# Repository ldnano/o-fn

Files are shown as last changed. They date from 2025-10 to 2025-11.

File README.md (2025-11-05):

<div align="center">

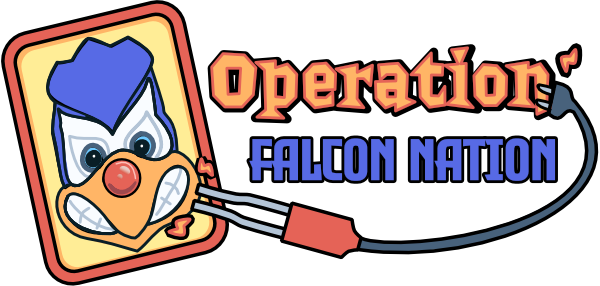
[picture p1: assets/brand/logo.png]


<h1>Operation: Falcon Nation</h1>

🦅 An automated board game reimagining which elevates scale, sensory experience, and interactivity. Featuring a life-size gameboard, themed pieces, and game mechanics, the project serves philanthropic causes and events.

----------------------------------
</div>

<details>
<summary><kbd>Table of contents</kbd></summary>

#### TOC

- [✨ Features](#-features)
- [🚀 Usage](#-urage)
  - [How to Operate](#how-to-operate)
  - [Game Mode Overview](#game-mode-overview)
  - [How to Play](#how-to-play)
- [📊 Flowcharts](#-flowcharts)
  - [Logic](#logic-)
  - [GUI](#gui-)
  - [Debugging](#debugging-)
- [🍱 Piece/Cavity Descriptions](#-piece-cavity-descriptions)
  - [List of pieces](#list-of-pieces)
  - [Cavity Anatomy](#cavity-anatomy)
- [💾 Programming Documentation](#-programming-documentation)
  - [Tasks](#tasks)
  - [Function Blocks](#function-blocks)
  - [Variables](#variables)
- [🔌 Electrical Wiring Diagram](#-electrical-wiring-diagram)
- [🗺 Monorepo Layout](#-monorepo-layout)

####

</details>

## ✨ Features

* Automatic piece-removal detection
* Circuit-based tong penalty loop
* Score-keeping and dynamic leaderboards
* Haptic-feedback-enabled modified kitchen tongs
* Multicolor board-and-cavity game state lights
* 11 custom-themed game pieces & cavities
* Two touchscreen web panel displays
* Two (repurposed car) speakers & immersive audio
* Plug-and-outlet power for project & tongs

## 🚀 Usage

### How to Operate

1. Plug in the power input located near the red switch on the left wall of the project, positioned closest near the falcon's head.
2. Press the red power switch located next to the power input and confirm that fans, web panels, and PLC (through glass) are powered and/or booting.
3. When the panel begins to display timers (typically 5 second countdowns), wait until a new calibration page with "LEFT" and "RIGHT" buttons. On the left panel, press "LEFT" and on the right one press "RIGHT".
4. The next page will be a sensor setup page that will indicate for which cavities the sensors are currently detecting a piece.
5. When all pieces are detected or early if necessary (pieces are lost, sensors are broken), press start and you will be navigated to the home (splash) screen.
6. From here, select a game mode and proceed through the steps of inputting player count, "nicknames", and confirmation.
7. Proceed to play Operation: Falcon Nation!

### Game Mode Overview

#### Demo Mode
In demo mode, a simplified "classic" mode variant, only four of the game's eleven total pieces are enabled, allowing a faster, more streamlined experience for showcases and demonstrations of the project.

#### Multiplayer (Classic) Mode
This version of the game operates most similarly to the original game, with all pieces activated. Without a stopwatch, the goal of this game is to compete for the highest monetary score.

#### Singleplayer (Blitz) Mode
As a singleplayer game, players of blitz mode aim to remove every piece in the least (or record) possible amount of time.

### How to Play

1. Presuming that game has been calibrated and configured, a "Play Game" button would become active on the left web panel screen.
2. When this button is clicked, the main game screen will appear, with the first player's piece assignment being displayed on the left panel and the initial (blank) leaderboard on the right.
3. This player must now attempt to take the assigned piece out of its cavity. If they fail, red lights will shine but if they succeed, green lights.
4, The leaderboard on the right will update with money counts accordingly and the "end game" button allows the game to be exited early.
5. When the game ends and the deck has been emptied, the final leaderboard and a thank you message will appear.

## 📊 Flowcharts

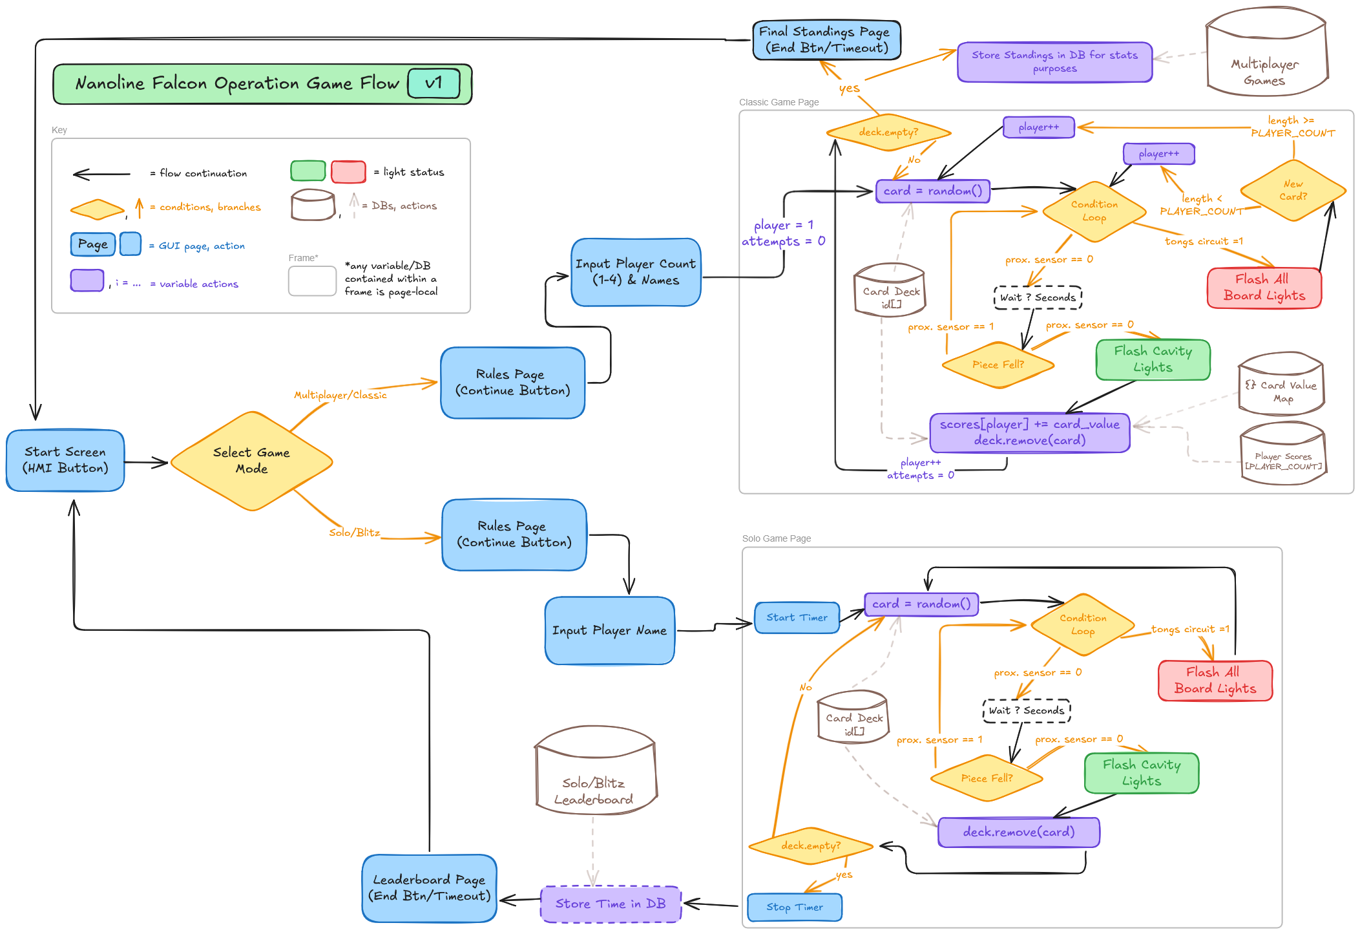
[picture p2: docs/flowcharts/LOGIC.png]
### <details><summary>Logic</summary> </details>

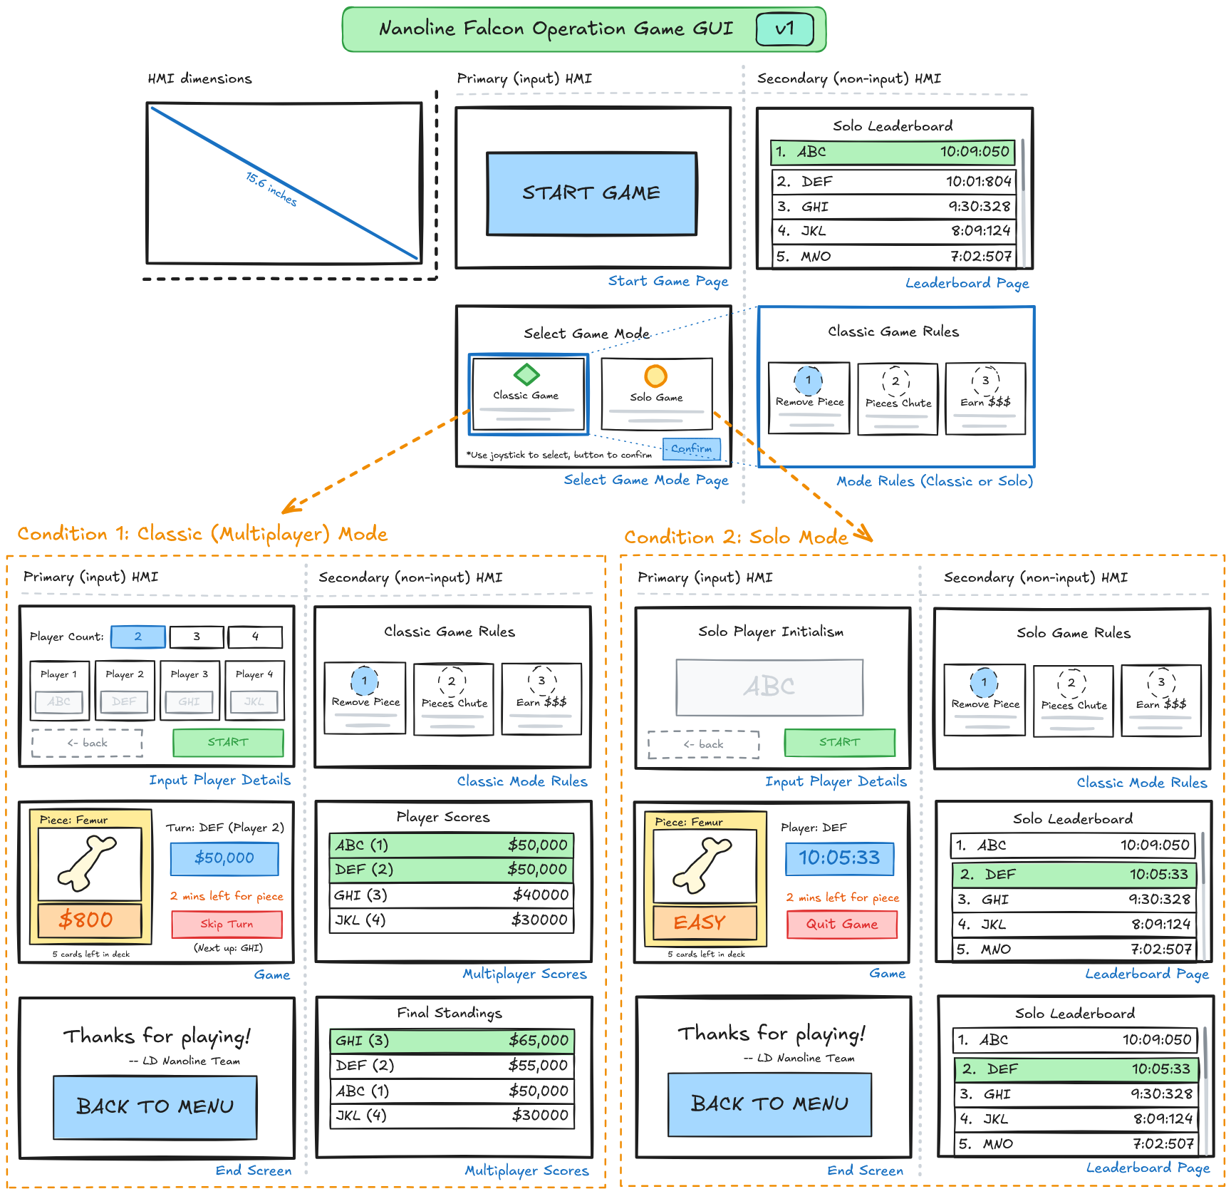
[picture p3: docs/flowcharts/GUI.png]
### <details><summary>GUI</summary> </details>

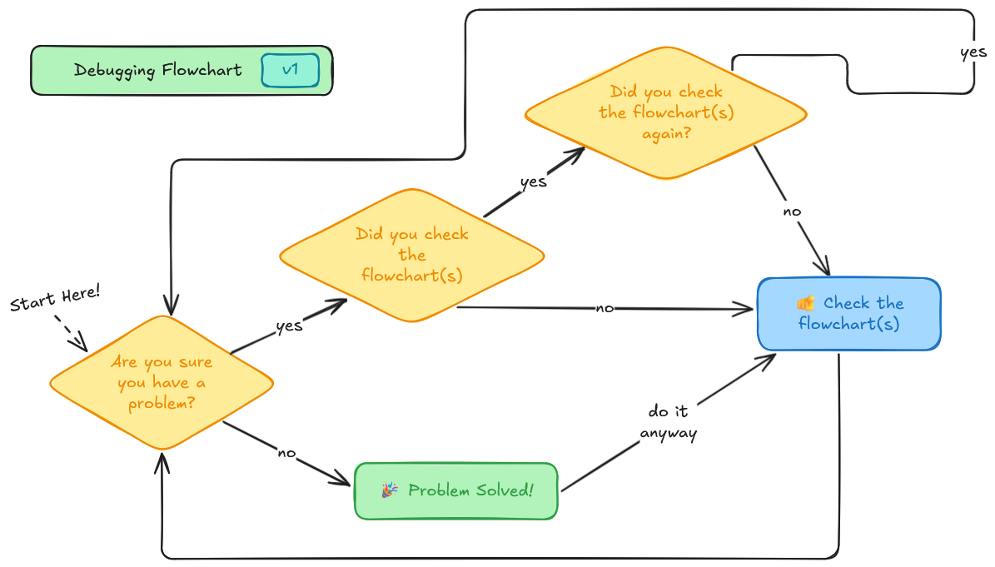
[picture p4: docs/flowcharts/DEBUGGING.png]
### <details><summary>Debugging</summary> </details>

## 🍱 Piece/Cavity Descriptions

### List of Pieces

| Piece Icon | Card Design | Name | Game Value |
|---|---|---|---|
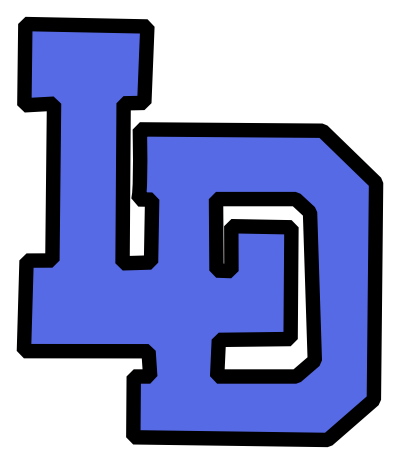
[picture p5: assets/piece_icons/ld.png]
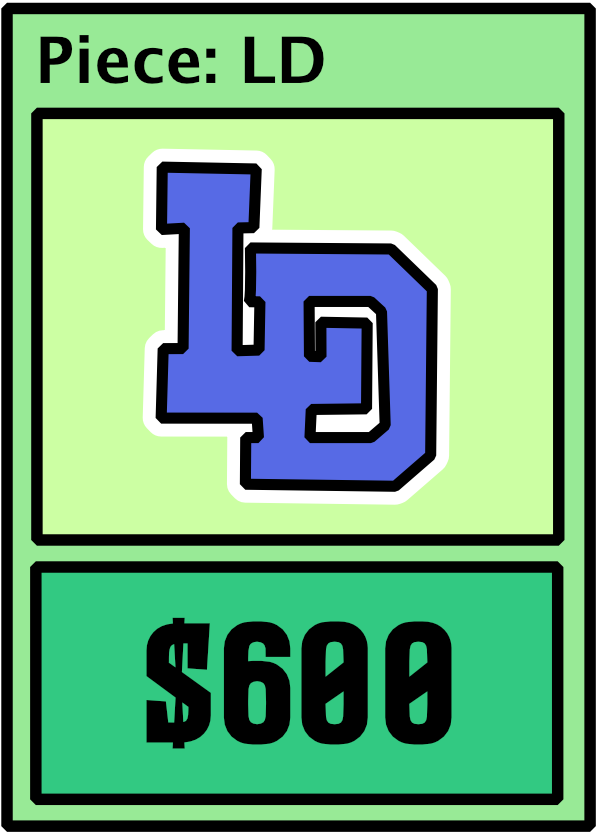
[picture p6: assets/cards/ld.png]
|  |  | LD Insignia | $600 |
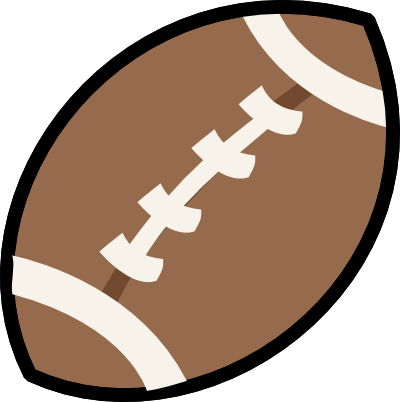
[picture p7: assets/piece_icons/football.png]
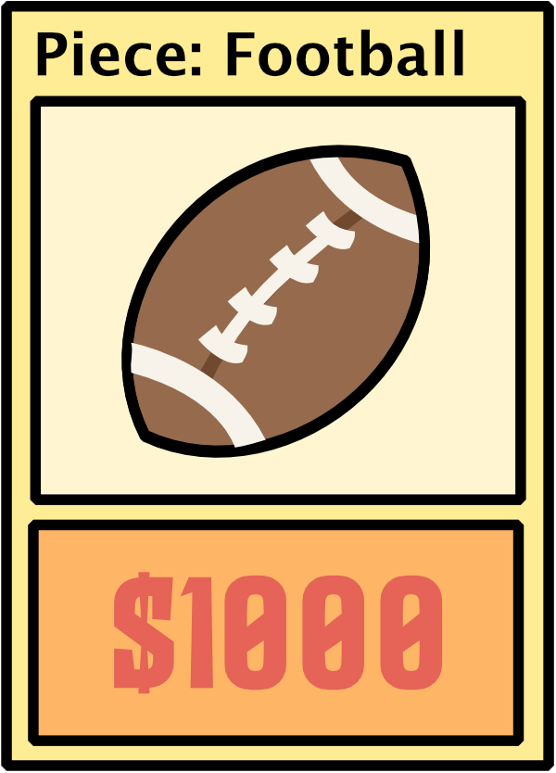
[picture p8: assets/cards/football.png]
|  |  | Football | $1000 |
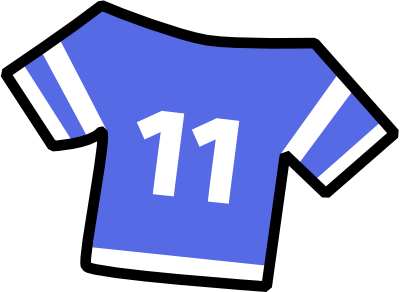
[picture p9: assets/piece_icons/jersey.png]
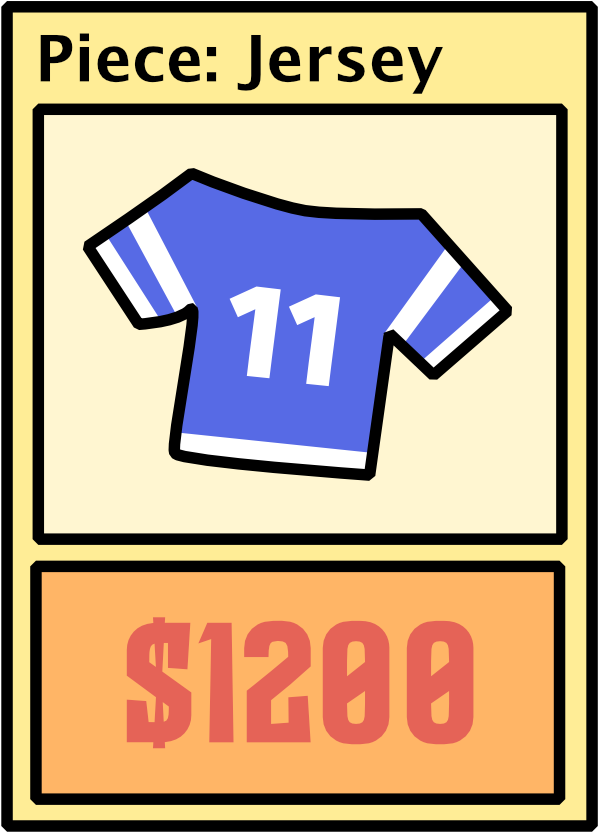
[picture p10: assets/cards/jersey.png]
|  |  | Jersey | $1200 |
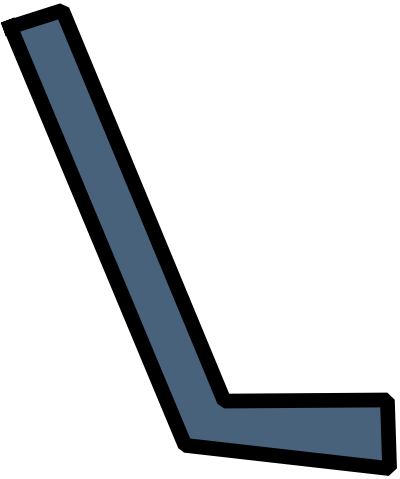
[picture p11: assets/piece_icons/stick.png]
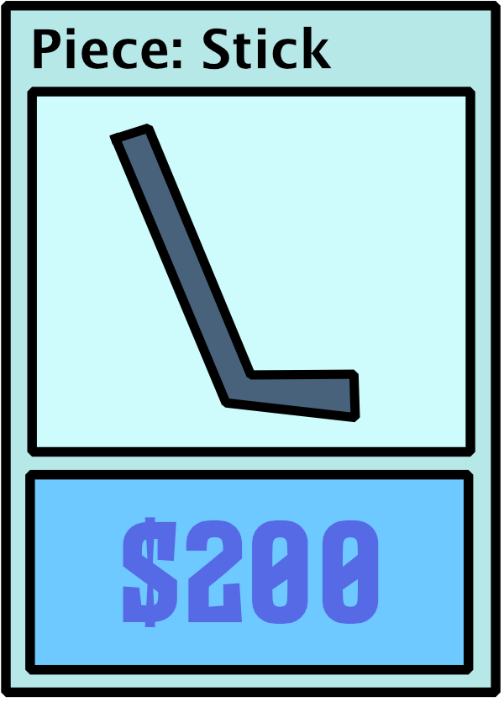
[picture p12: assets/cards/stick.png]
|  |  | Hockey Stick | $200 |
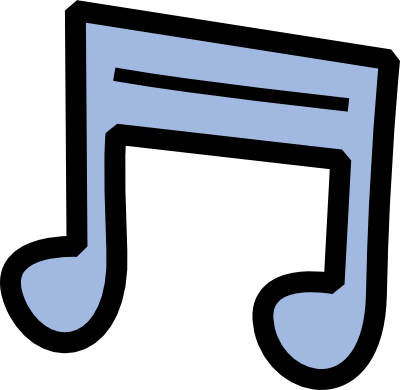
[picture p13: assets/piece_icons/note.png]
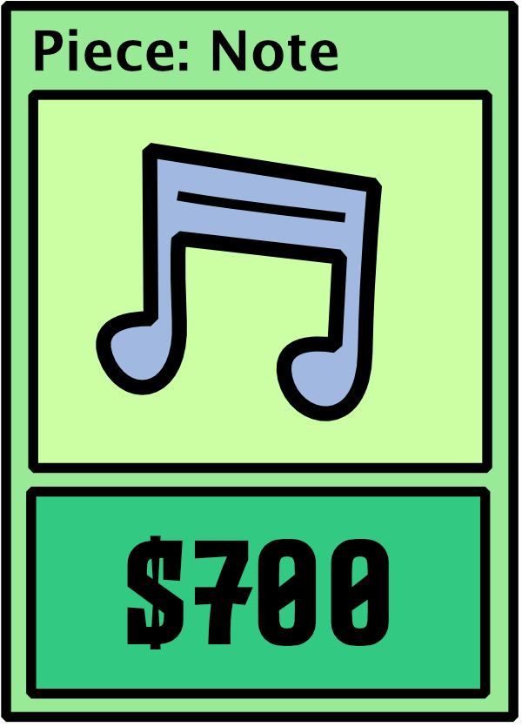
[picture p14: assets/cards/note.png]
|  |  | Music Note | $700 |
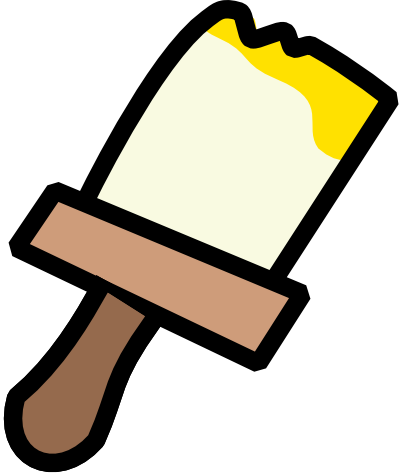
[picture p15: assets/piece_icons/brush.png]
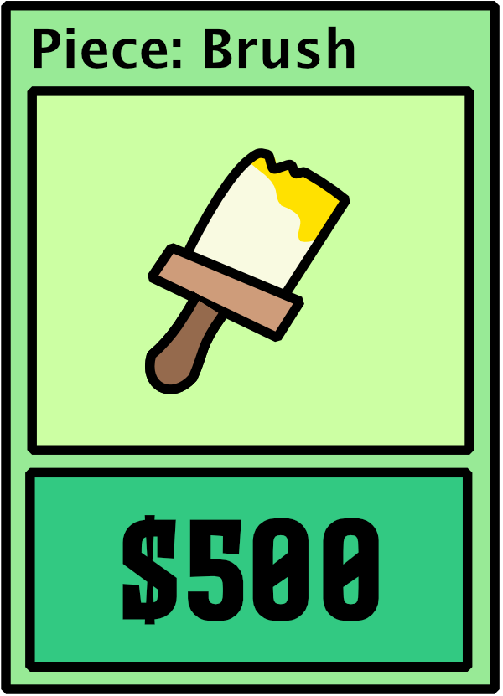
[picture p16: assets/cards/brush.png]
|  |  | Paintbrush | $500 |
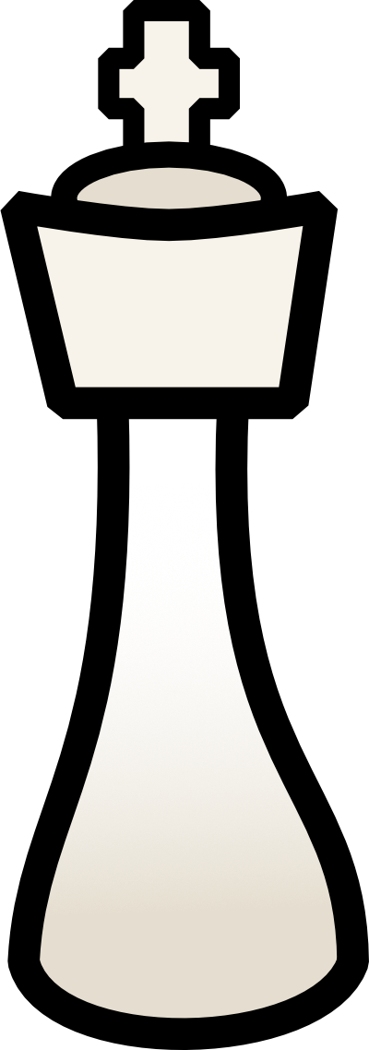
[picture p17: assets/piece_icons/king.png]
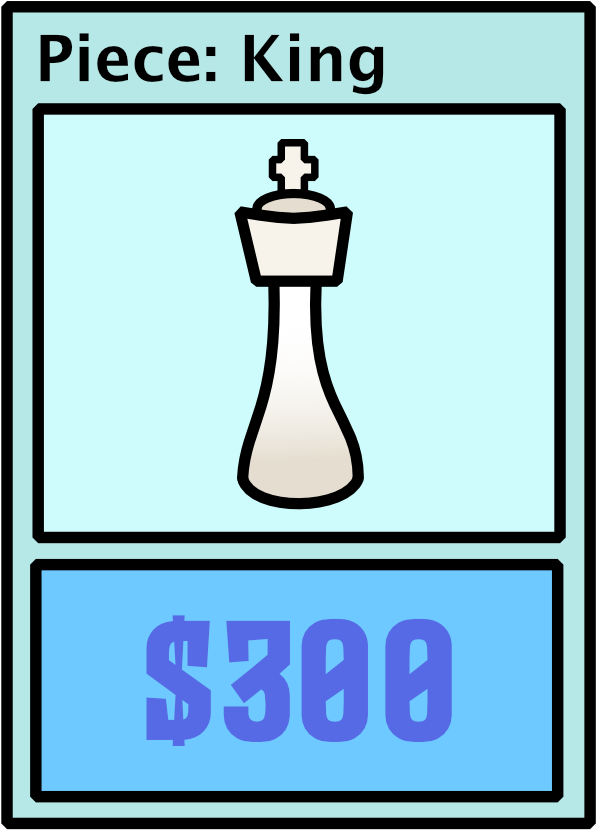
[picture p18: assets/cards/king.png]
|  |  | Chess King | $300 |
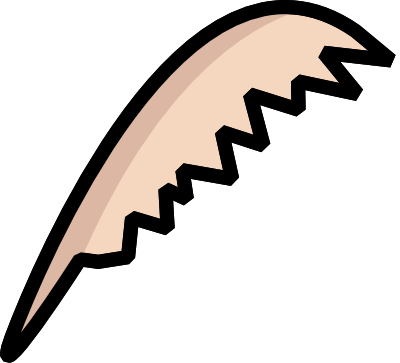
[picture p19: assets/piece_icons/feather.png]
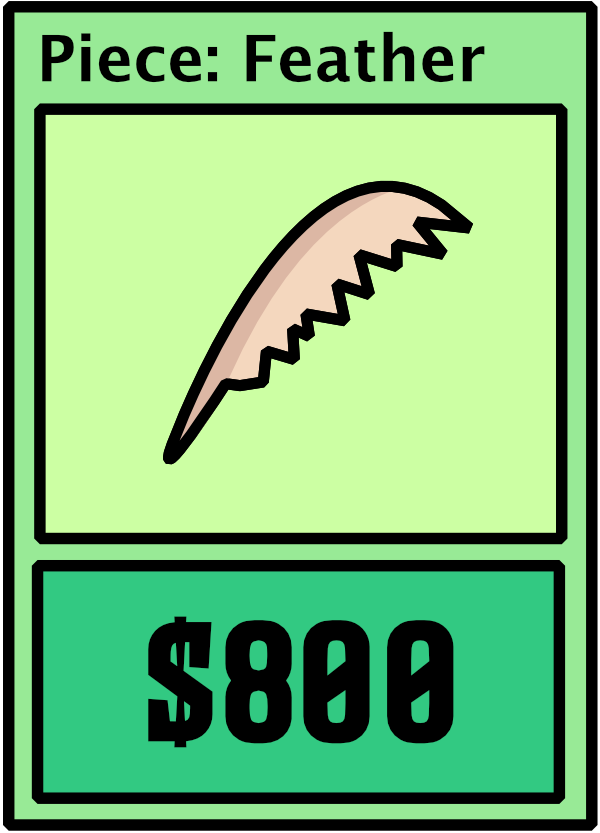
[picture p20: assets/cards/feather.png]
|  |  | Feather | $800 |
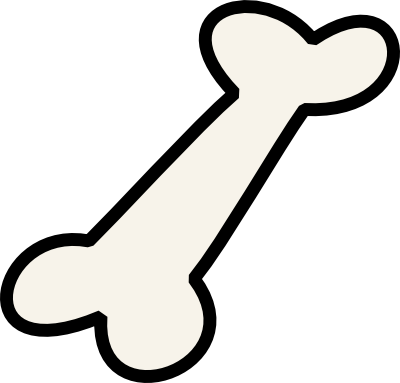
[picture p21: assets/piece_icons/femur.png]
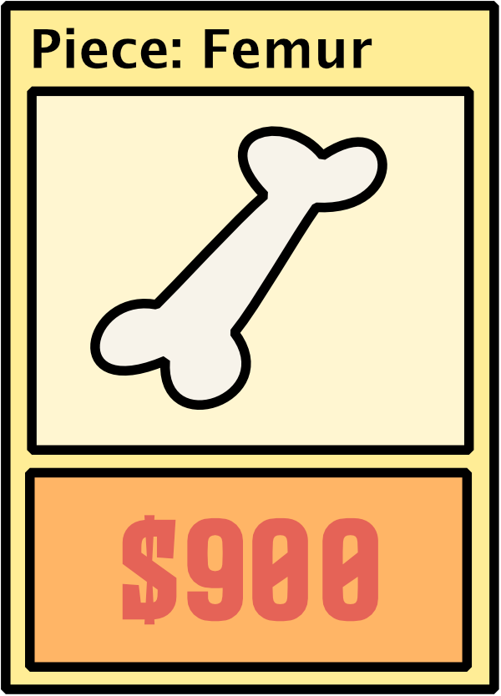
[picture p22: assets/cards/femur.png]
|  |  | Bone | $900 |
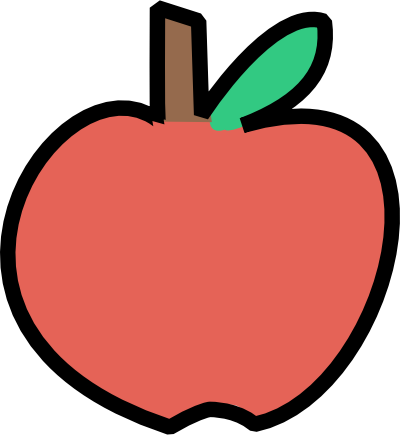
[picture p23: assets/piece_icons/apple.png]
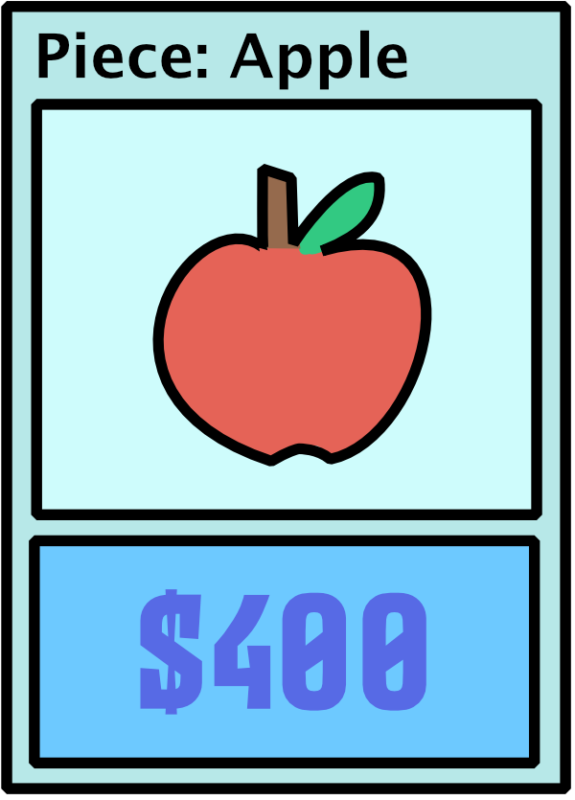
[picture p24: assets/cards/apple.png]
|  |  | Apple | $400 |
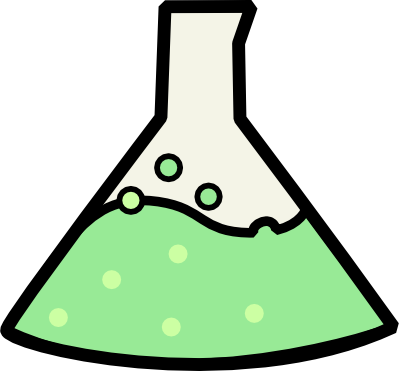
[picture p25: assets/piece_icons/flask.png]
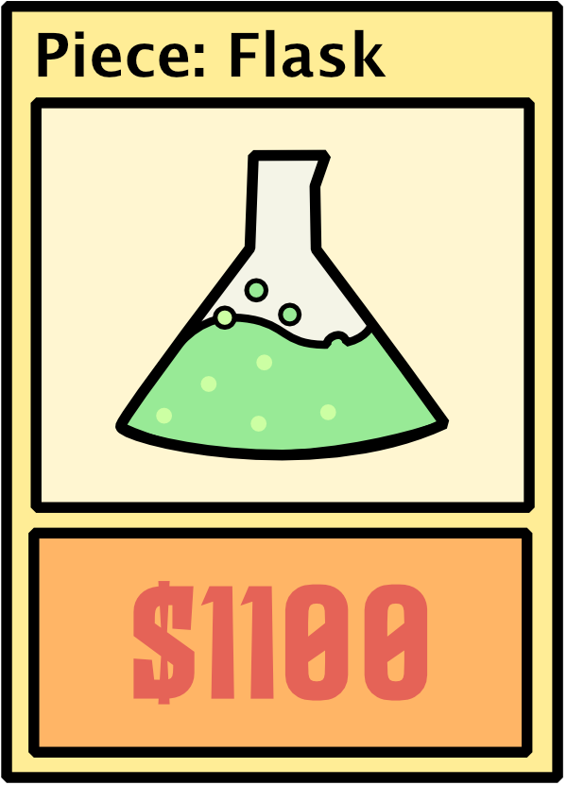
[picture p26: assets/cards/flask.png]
|  |  | Flask | $1100 |

### Cavity Anatomy

(Top-to-bottom)

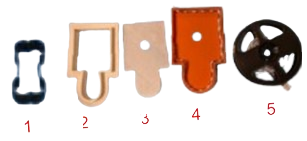
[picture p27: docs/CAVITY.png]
Cavity Diagram


1. Conductive Cavity Wall
2. Cavity Bracket
3. Clear "Light Refractor" Panel
4. Cavity Light Shell
5. Light Strip in Channel

## 💾 Programming Documentation

### Tasks

#### `Main`
- **Type:** Cyclic (100 ms)
- **Description:** Runs all game functions depending on what part of game player is at

#### `Sounds`
- **Type:** Cyclic (100 ms)
- **Description:** Receives variable changes and triggers MP3 trigger outputs to play game sounds

#### `Startup`
- **Type:** Startup
- **Description:** Resets variables and sets constants

### Function Blocks

- **`CalcWinningPlayer`** - Calculates which player(s) is winning to display on HMI and decide on winners

- **`CheckAllPiecesInCavity`** - Checks whether all distance sensors are activated to determine whether game is ready to start

- **`CheckPieceInCavity`** - Checks whether a specific piece's distance sensor is activated

- **`CheckTouchingCavity`** - Checks whether the tongs are touching a piece's conductive sides

- **`DealWithPiece`** - For the current target piece, checks whether touching the cavity and whether the piece has been removed, then triggers either success or failure of piece

- **`FormatName`** - Formats a player's name to be all caps and a maximum of three letters long

- **`GetNewPiece`** - Randomly assigns a new piece and a new target player to remove it; if all pieces have been removed, ends game

- **`LightEmptyCavities`** - Lights up the cavities that are empty with white and those with pieces in green

- **`MultiPlayerLoop`** - Sets target player variables for HMI and runs `DealWithPiece` for the current piece
  
- **`NumPiecesInCavities`** - Gets the number of cavities that currently contain pieces

- **`RandomNumber`** - Generates and returns a random number, capped at a provided maximum

- **`ResetBetweenGames`** - Resets game variables before each game

- **`SetAllLights`** - Utility, sets the colors of all lights to the colors specified as inputs

- **`SetHMIPiecevars`** - Utility, sets variables linked to HMI tags for distance sensors

- **`SetLights`** - Utility, sets lights for a specific cavity in inputs colors

- **`UppercaseLetter`** - Utility, converts letter to all uppercase

### Variables

#### Light Outputs
- **`cav{#}{color}`** - Each cavity has 4 boolean variables for RGBA where {#} is an integer 1-11 and {color} is red, green, blue, or white
- **`board{color}`** - There are 4 boolean variables for the entire board's lighting

#### Sound Outputs
- **`{sound_name}_sound_out`** - There are 9 boolean variables for controlling sound where sound_name is intro, hawk, fail, success, winner, or p{num} where {num} is an integer 1-4

#### HMI Page Variables and Flags
- **`CurrentPage`** - Current page identifier
- **`P{piece_num}_in`** - Variables linked to HMI tags for each piece's distance sensor
- **`HMInum`** - Integer representing which HMI panel is being run (1 or 2)
- **`simulator_touched_sides`** - Simulator variable for testing
- **`simulator_piece_in_cav`** - Simulator variable for testing
- **`EndGameEarly`** - Boolean representing whether end game early button has been clicked

---

## 🔌 Electrical Wiring Diagram

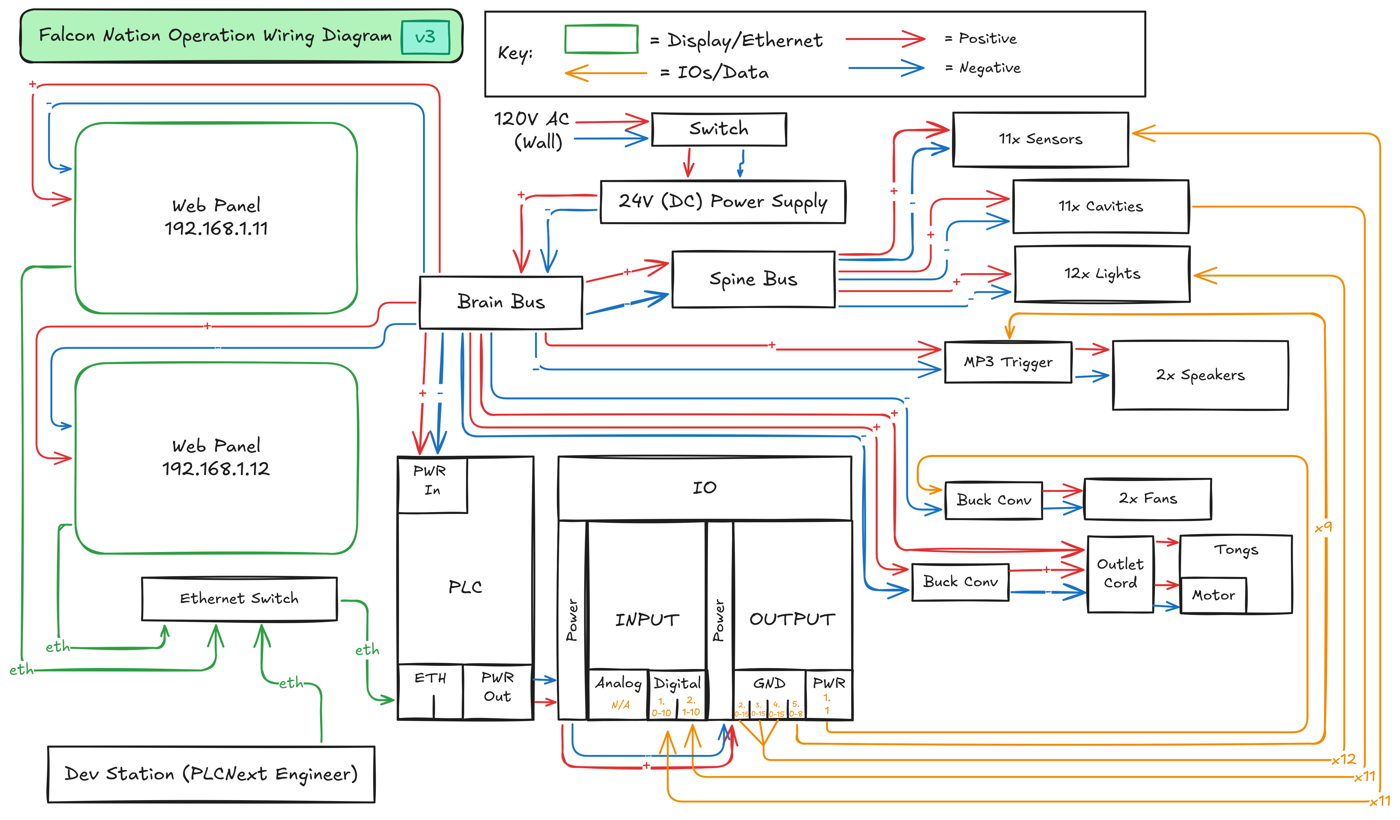
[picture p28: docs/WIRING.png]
Electrical Wiring Diagram


### 🗺 Monorepo Layout

This monorepo includes all of the components of the project one would need to reproduce, update, or extend the original version contained within. The specific documentation most relevant to this objective are:

* `/src` - The PLCNext Engineer project codebase
* `/docs/WIRING.png` - The electrical wiring configuration
* `/3d` - The 3d-print-ready piece and cavity files
* `/diy` - The wood, glass, tong, and vinyl construction (WIP)
* `/assets` - Files related to art, SFX, music, and branding
* `/diy/EXPENSES.md` - A budgeted list of components (& sources!)

__Operation: Falcon Nation - An LD Nano Team Production__

[back-to-top]: https://img.shields.io/badge/-BACK_TO_TOP-black?style=flat-square

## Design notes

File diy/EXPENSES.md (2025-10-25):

# 💵 Expenses

##

## Team Expenses

| Date | Category | Item | Quantity | Cost | Source | Link |
|---|---|---|---|---|---|---|
| 2/10 | Electronics | BTF LED Light Strips | 2 spools | $24.37 | Amazon | [Link](https://www.btf-lighting.com/products/1-sk6812-rgbw-4-in-1-pixels-individual-addressable-led-strip-dc5v) |
| 2/25 | Audio | SparkFun MP3 Trigger | 1 unit | $54.00 | Amazon | [Link](https://www.amazon.com/SparkFun-4334427041-MP3-Trigger/dp/B01BHHBJ4K) |
| 3/19 | 3D Printing | ProtoPasta Conductive Filament | 2 spools | $100.00 | Amazon | [Link](https://www.amazon.com/Protopasta-Electrically-Conductive-Compatible-FlashForge/dp/B00X8BQYVM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) |
| 3/21 | Sensors | Proximity Sensors | 11 units | $76.20 | Amazon | [Link](https://www.amazon.com/Taiss-LJC18A3-H-Z-Capacitance-Proximity-NO%EF%BC%88Normally/dp/B0746FYF5S) |
| 3/21 | 3D Printing | Clear Filament | 1 spool | $19.07 | Amazon | |
| 3/24 | Materials | Wood & Stain | - | $48.72 | Lowe's | |
| 3/25 | Materials | Wood & Supplies | - | $31.79 | Lowe's | |
| 3/27 | Electronics | Bluetooth Module | 1 unit | $13.78 | Amazon | |
| 3/27 | Miscellaneous | Metal Tongs | 2 units | $10.00 | Amazon | |
| 3/31 | Branding | Falcon Mascot Vinyl | 1 set | $118.72 | Local | *Originally quoted at $99* |
| 4/4 | Branding | Team T-Shirts | Multiple | $195.65 | Local | |
| 4/9 | Electronics | Vetroo Blue LED Computer Fans | 2 units | $26.67 | Amazon | [Link](https://vetroo.com/collections/case-fan/products/vetroo-df120-case-fan-kit?variant=43537804722410) |
| 4/10 | Electronics | Rocker Power Switch | 1 unit | $8.47 | Amazon | [Link](https://www.amazon.com/DaierTek-Rocker-Switch-Lighted-Motorcycle/dp/B07S914SFBy) |
| 4/10 | Electronics | Additional BTF LED Light Strips | - | (included) | Amazon | *For cavity lighting* |
| 4/11 | Electronics | DC Motor & 4-Color Wire | 1 set | $34.21 | Amazon | *For haptic feedback* |
| 4/16 | Miscellaneous | Foam Corner Cushions | 12 units | $12.00 | Amazon | [Link](https://www.amazon.com/Corner-Protector-Protectors-Fireplace-Furniture/dp/B0DHVZN7Q1) |
| 4/17 | Audio | Pemenol MP3 Trigger Amplifier | 1 unit | $18.00 | Amazon | [Link](https://www.amazon.com/Playback-PEMENOL-Trigger-Amplifier-Christmas/dp/B0C9J7XGW6) |
| 4/18 | Audio | Acoustik Car Speakers (120W) | 2 units | $36.00 | Amazon | [Link](https://www.amazon.com/Sealed-Range-Audio-Speaker-XPS-104/dp/B07TS4XWJJ) |
| - | Materials | Acrylic Plexiglass | Multiple sheets | **FREE** | Local | *Donated* |

---

## Expense Summary by Category

| Category | Items | Total Cost | Notes |
|---|---|---|---|
| **Audio System** | MP3 Trigger, Amplifier, Speakers | $108.00 | SparkFun trigger fried 4/17; replaced with Pemenol |
| **Sensors** | Proximity sensors | $76.20 | 11 capacitance proximity sensors |
| **3D Printing** | Conductive & clear filament | $119.07 | Conductive ($50/spool) for cavity inputs |
| **Structural Materials** | Wood, stain, acrylic | $80.51 | Free acrylic from Weaver Glass |
| **Electronics** | LED strips, fans, motor, switch, Bluetooth | $93.72 | Includes haptic feedback motor |
| **Branding** | Vinyl mascot, team t-shirts | $314.37 | Vinyl quotes increased from $99 to $118.72 |
| **Miscellaneous** | Tongs, corner cushions | $22.00 | Metal tongs with motor covers |
| **TOTAL EXPENSES** | | **$813.87** | |

---

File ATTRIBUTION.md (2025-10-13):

# Attribution

## Sound Attribution:

* “Player [1-4]” and “Winner!” by Kenney.nl
* “Success Fanfare Trumpets” by freesound_community from Pixabay
* “success 1” by  freesound_community from Pixabay
* “Buzzer 5” by floraphonic from Pixabay
* “TV Show Intro Music” by TheoJT from Pixabay
* “Screaming Hawk” by PsychoBird on SoundBible

## Tools/Software Used:

* Affinity Designer for Visual Design (Vinyl Vectors, T-Shirts, Project/Team Logos, Card Icons)
* Audacity for sound editing/modifications
* PLCNext Engineer for programming/simulation/testing
* Excalidraw for diagramming, flowcharting

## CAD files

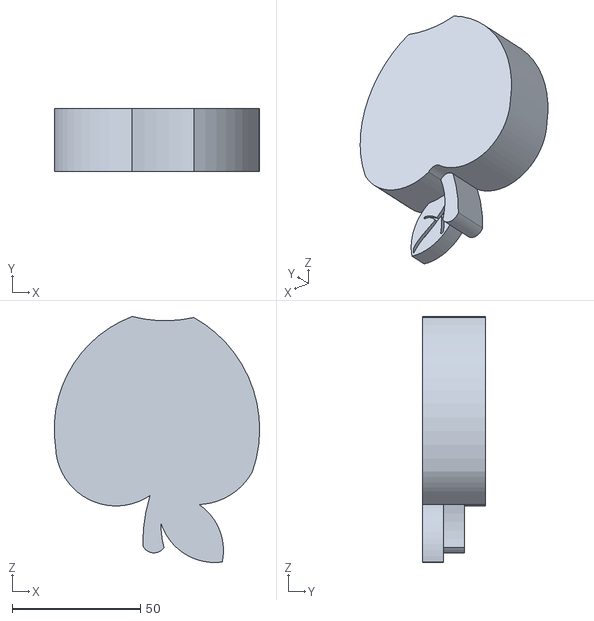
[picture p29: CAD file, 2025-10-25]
3d/apple/piece.stl
79.9 x 24.7 x 95.8

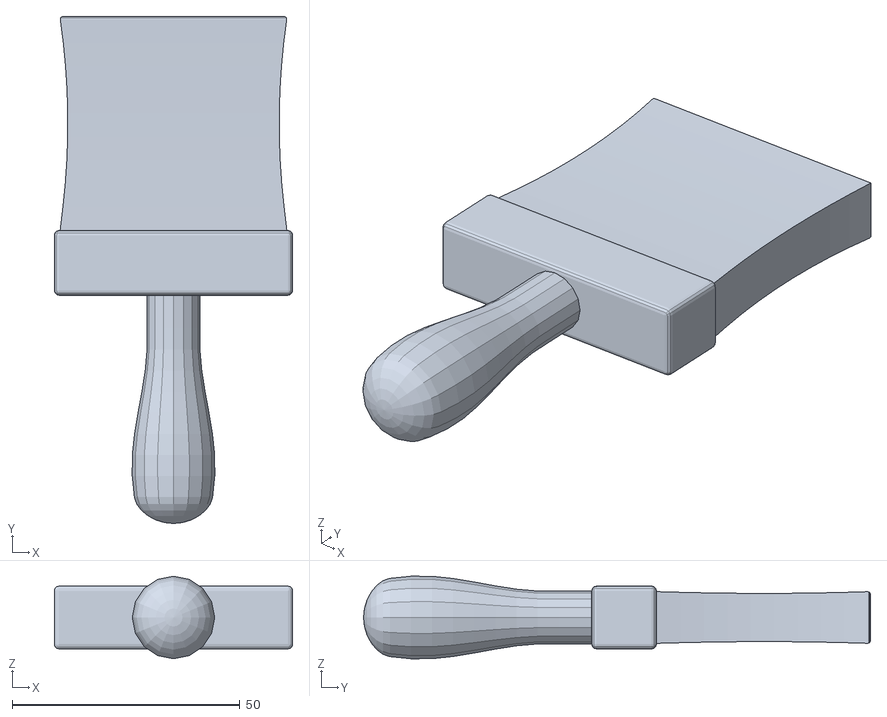
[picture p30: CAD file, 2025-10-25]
3d/brush/piece.stl
52.3 x 111.3 x 18.1

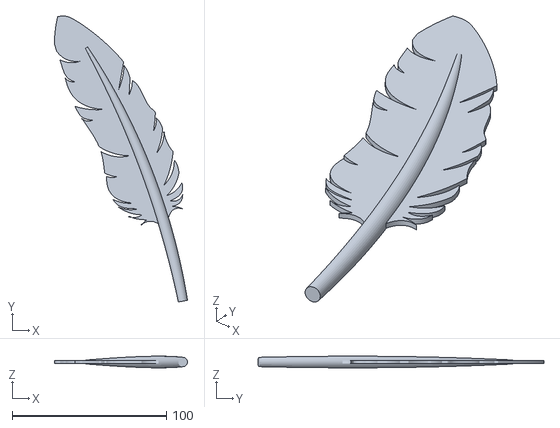
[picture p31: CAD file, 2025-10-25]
3d/feather/piece.stl
86.2 x 185.3 x 7.56

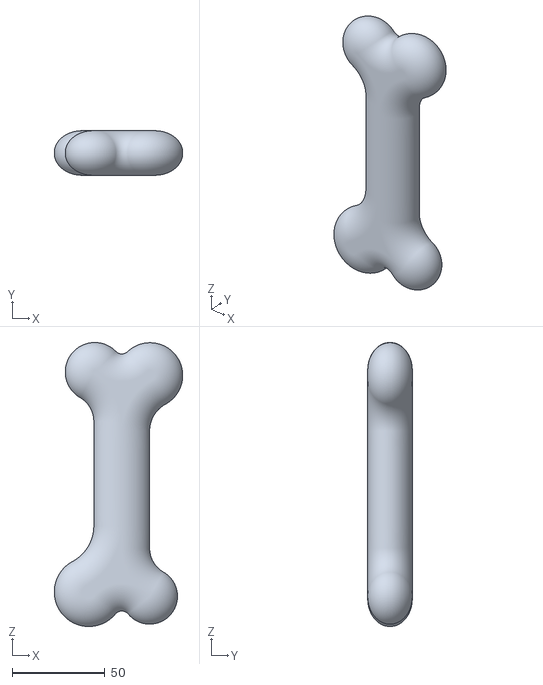
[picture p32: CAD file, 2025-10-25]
3d/femur/piece.stl
69.2 x 24.0 x 153.0

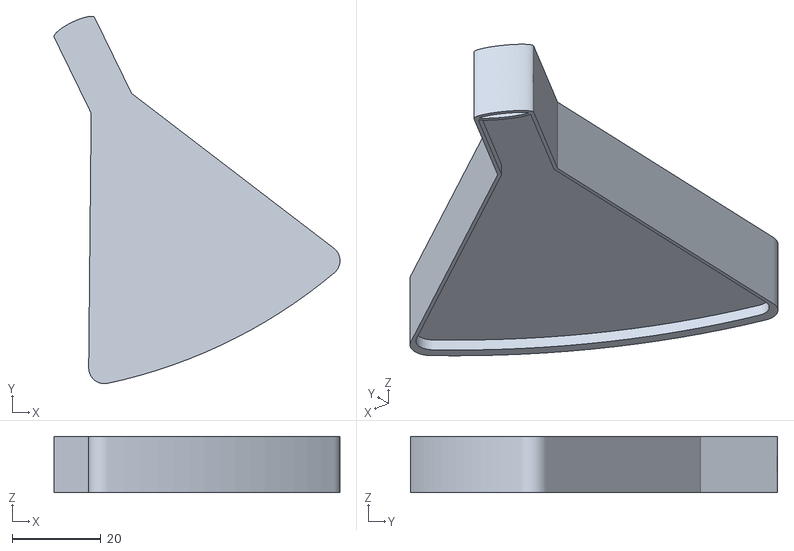
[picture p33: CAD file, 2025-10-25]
3d/flask/piece.stl
64.5 x 82.9 x 12.7

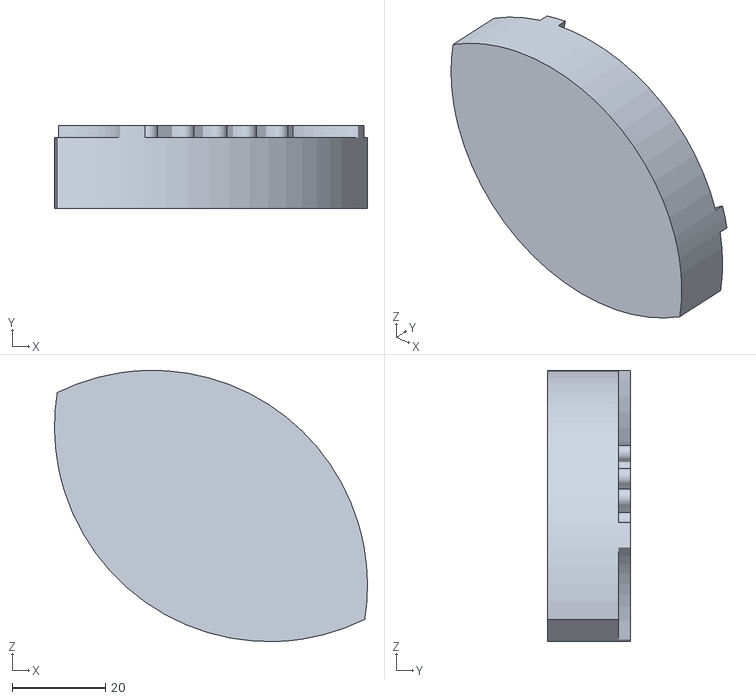
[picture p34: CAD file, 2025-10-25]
3d/football/piece.stl
67.2 x 17.8 x 58.2

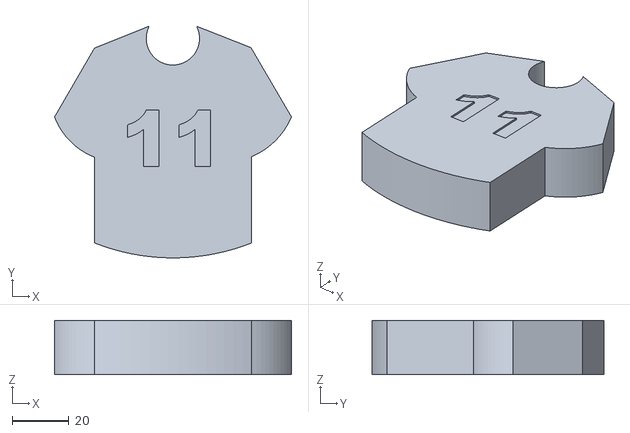
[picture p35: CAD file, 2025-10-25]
3d/jersey/piece.stl
83.3 x 81.4 x 19.0

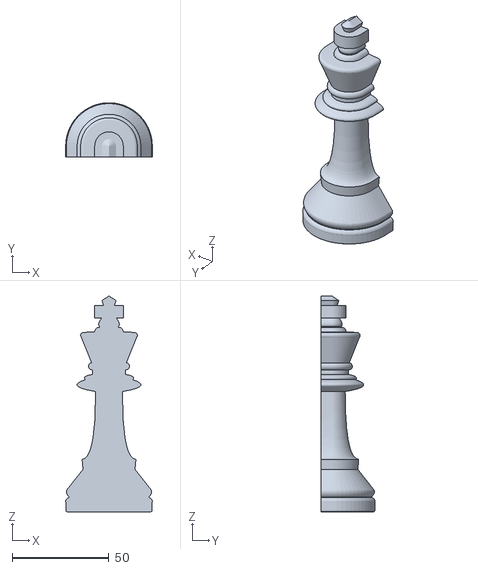
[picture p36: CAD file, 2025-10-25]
3d/king/piece.stl
44.9 x 28.1 x 111.7

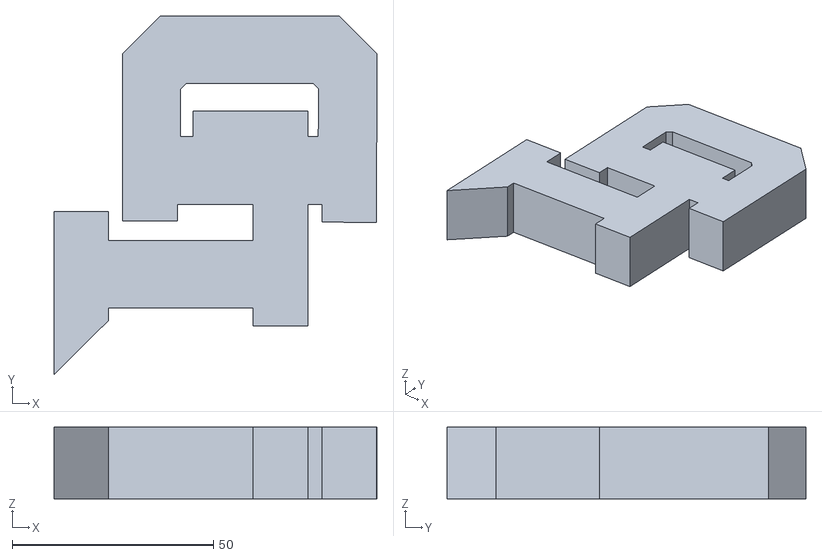
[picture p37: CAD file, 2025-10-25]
3d/ld/piece.stl
80.2 x 89.0 x 17.8

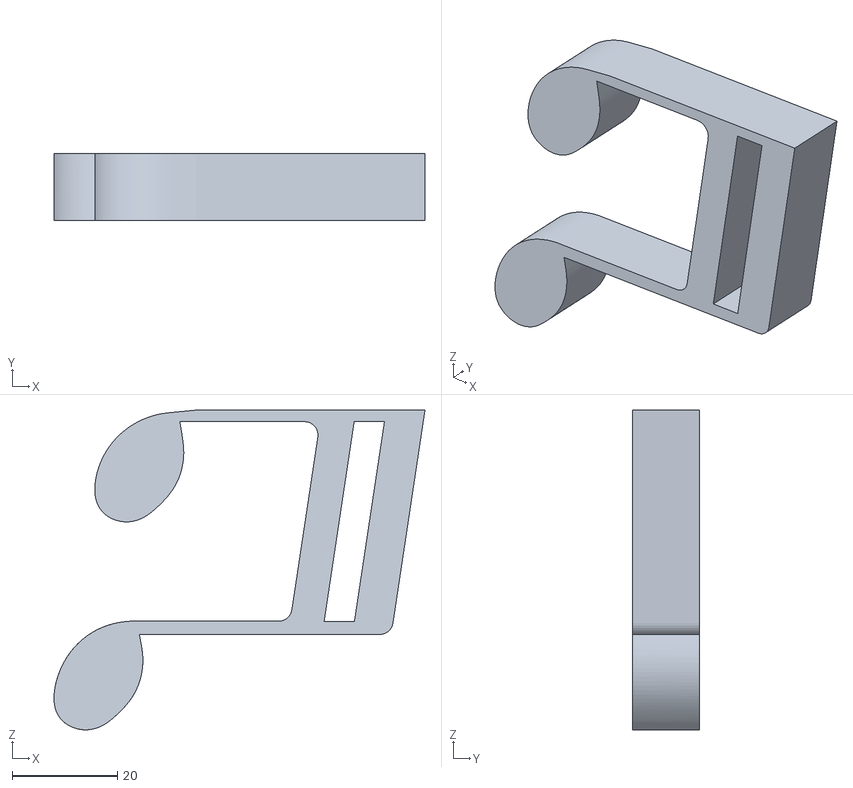
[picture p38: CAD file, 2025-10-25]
3d/note/piece.stl
70.4 x 12.7 x 60.7

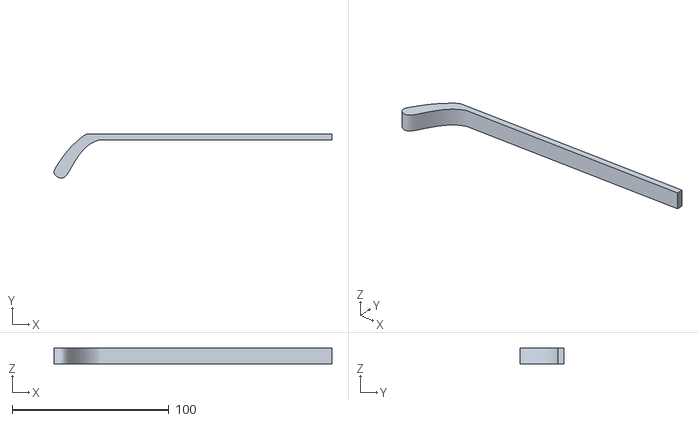
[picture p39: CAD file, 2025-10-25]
3d/stick/piece.stl
177.3 x 28.4 x 10.2

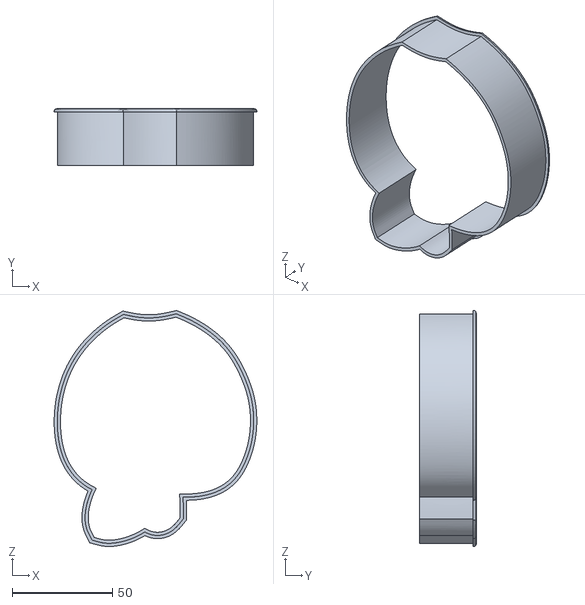
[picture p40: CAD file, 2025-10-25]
3d/apple/conductive.stl
101.3 x 28.3 x 117.9

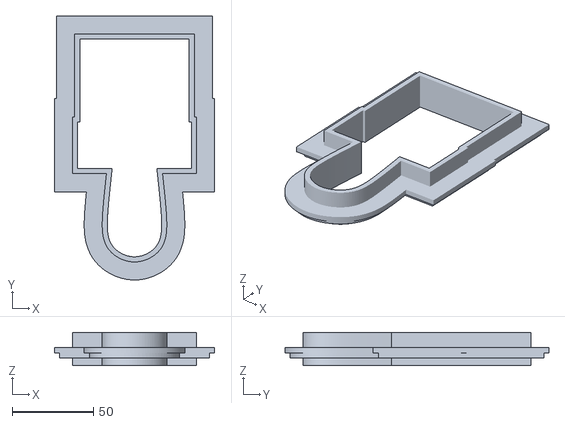
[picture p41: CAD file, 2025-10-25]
3d/brush/top.stl
98.7 x 162.7 x 20.6

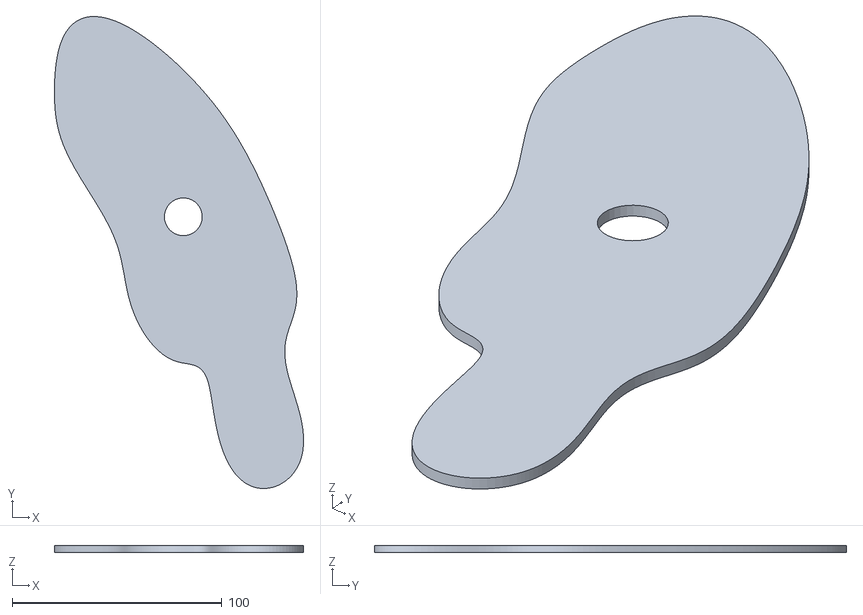
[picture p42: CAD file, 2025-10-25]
3d/feather/clear.stl
118.9 x 225.2 x 3.18

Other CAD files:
3d/femur/conductive.stl
3d/flask/clear.stl
3d/football/clear.stl
3d/jersey/conductive.stl
3d/apple/bottom.stl
3d/apple/clear.stl
3d/apple/top.stl
3d/brush/bottom.stl
3d/brush/clear.stl
3d/brush/conductive.stl
3d/feather/bottom.stl
3d/feather/conductive.stl
3d/feather/top.stl
3d/femur/bottom.stl
3d/femur/clear.stl
3d/femur/top.stl
3d/flask/bottom.stl
3d/flask/conductive.stl
3d/flask/top.stl
3d/football/bottom.stl
3d/football/conductive.stl
3d/football/top.stl
3d/jersey/bottom.stl
3d/jersey/clear.stl
3d/jersey/top.stl
3d/king/bottom.stl
3d/king/clear.stl
3d/king/conductive.stl
3d/king/top.stl
3d/ld/bottom.stl
3d/ld/clear.stl
3d/ld/conductive.stl
3d/ld/top.stl
3d/note/bottom.stl
3d/note/clear.stl
3d/note/conductive.stl
3d/note/top.stl
3d/stick/bottom.stl
3d/stick/clear.stl
3d/stick/conductive.stl
3d/stick/top.stl

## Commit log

2025-10-25 :bento: Add 3d print files & card assets
    [bottom.stl, clear.stl, conductive.stl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]
2025-10-25 :bento: Add 3d piece files
    [piece.stl]
